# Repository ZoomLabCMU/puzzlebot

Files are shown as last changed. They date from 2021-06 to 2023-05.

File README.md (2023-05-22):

# PuzzleBots: Physical Coupling of Robot Swarms
Sha Yi, Zeynep Temel, Katia Sycara

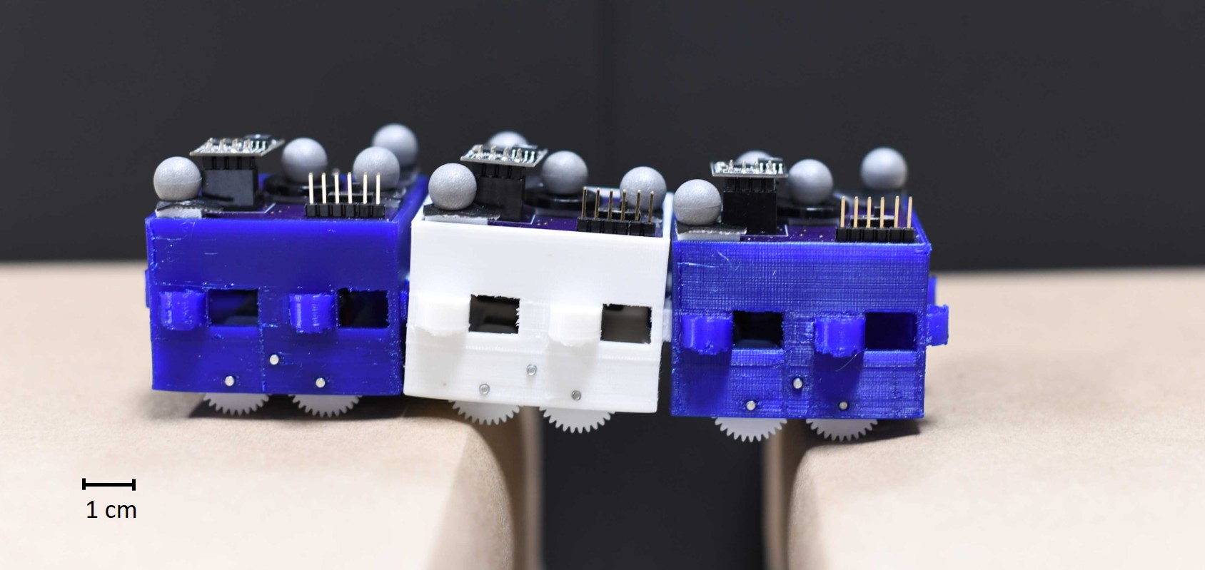
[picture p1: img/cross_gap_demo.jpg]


Link to our [video](https://www.youtube.com/watch?v=QP3eMZXLSw4). We present a guide to make and run our PuzzleBots. A newer version is available [here](https://github.com/ZoomLabCMU/puzzlebot_v2).  

If you find our work useful, please consider citing our paper:  
```
@inproceedings{yi2021puzzlebots,
  title={PuzzleBots: Physical Coupling of Robot Swarms},
  author={Yi, Sha and Temel, Zeynep and Sycara, Katia},
  booktitle={2021 IEEE International Conference on Robotics and Automation (ICRA)},
  pages={8742--8748},
  year={2021},
  organization={IEEE}
}
```

**Software Requirement**
- python
- ROS
- Arduino

**Hardware Requirement**
- 3D Printer
- Soldering Iron
- Circuit Board Production (may use external manufacturer)
- Vicon (or other localization systems)

## Preparation
1. Assemble the robot based on instructions from the [assembly page](docs/assembly.md).
2. Burn bootloader of Arduino Pro Mini (8M, 3.3V) to the ATMega328P.
3. Configure ESP8266 WiFi module with baud rate to be 9600.

## Run the Demo
### Setup
1. Configure the system  
Change Line 83 and 105 in `code/puzzlebot_arduino/wifitcp_motor_only/wifitcp_motor_only.ino` to your own wifi and IP address.
2. Load program onto circuit board  
Open the program `code/puzzlebot_arduino/wifitcp_motor_only/wifitcp_motor_only.ino` in Arduino Studio (or other Software) and load to the circuit board built in [assembly page](docs/assembly.md).
3. Build ROS package  
Copy `code/puzzlebot_control/` into the ROS catkin source directory. Build the package.

### Run
Each robot is associated with an IP address. In our setting, robot IP address has the form `192.168.0.20[ROBOT_ID]`. The corresponding Vicon ROS topic thus has the form `vicon/p20[ROBOT_ID]/p20[ROBOT_ID]`. For example, robot #2 has an IP of `192.168.0.202`, and the corresponding vicon topic is `vicon/p202/p202`.  
This can be changed in `code/puzzlebot_control/src/puzzlebot_control/hardware_wrap.py` Line 33. To turn off the vicon callback, change Line 30 in the `hardware_wrap.py` file.

Before launching the puzzlebot node, make sure the Vicon (or other localization system) is running and publishing the corret ROS topics. Then do
```
rosrun puzzlebot_control run_hardware.py [NUMBER_OF_ROBOTS]
```
For example, with three robots, run `rosrun puzzlebot_control run_hardware.py 3`.

Then, switch on the robots by sliding the switch on the top. You are expected to see the ESP8266 LED flashes then the console will show robots are connected in sequence. The program will start once all robots are connected.

### Testing Functions
A testing function `keyboard_input_lr` is provided in `robot.py`. It can be called in `hardware_wrap.py` to send velocity command during runtime to the robots to help debug hardware issues.

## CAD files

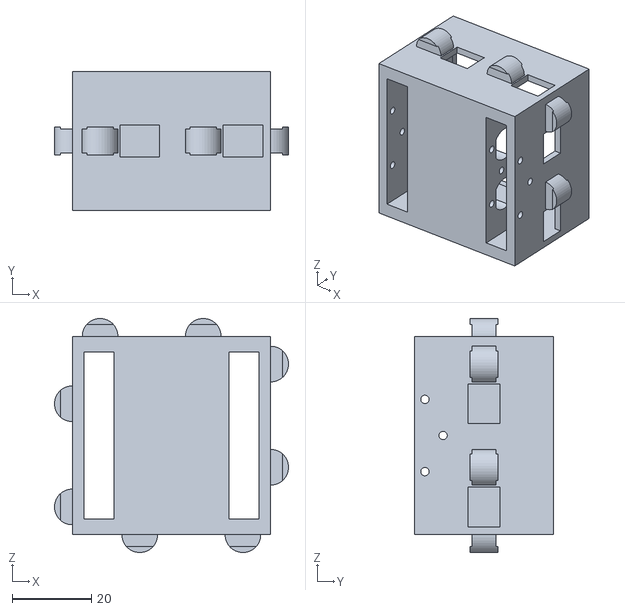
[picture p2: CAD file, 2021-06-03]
files/puzzlebot_chasis.STL
59.0 x 35.0 x 59.0

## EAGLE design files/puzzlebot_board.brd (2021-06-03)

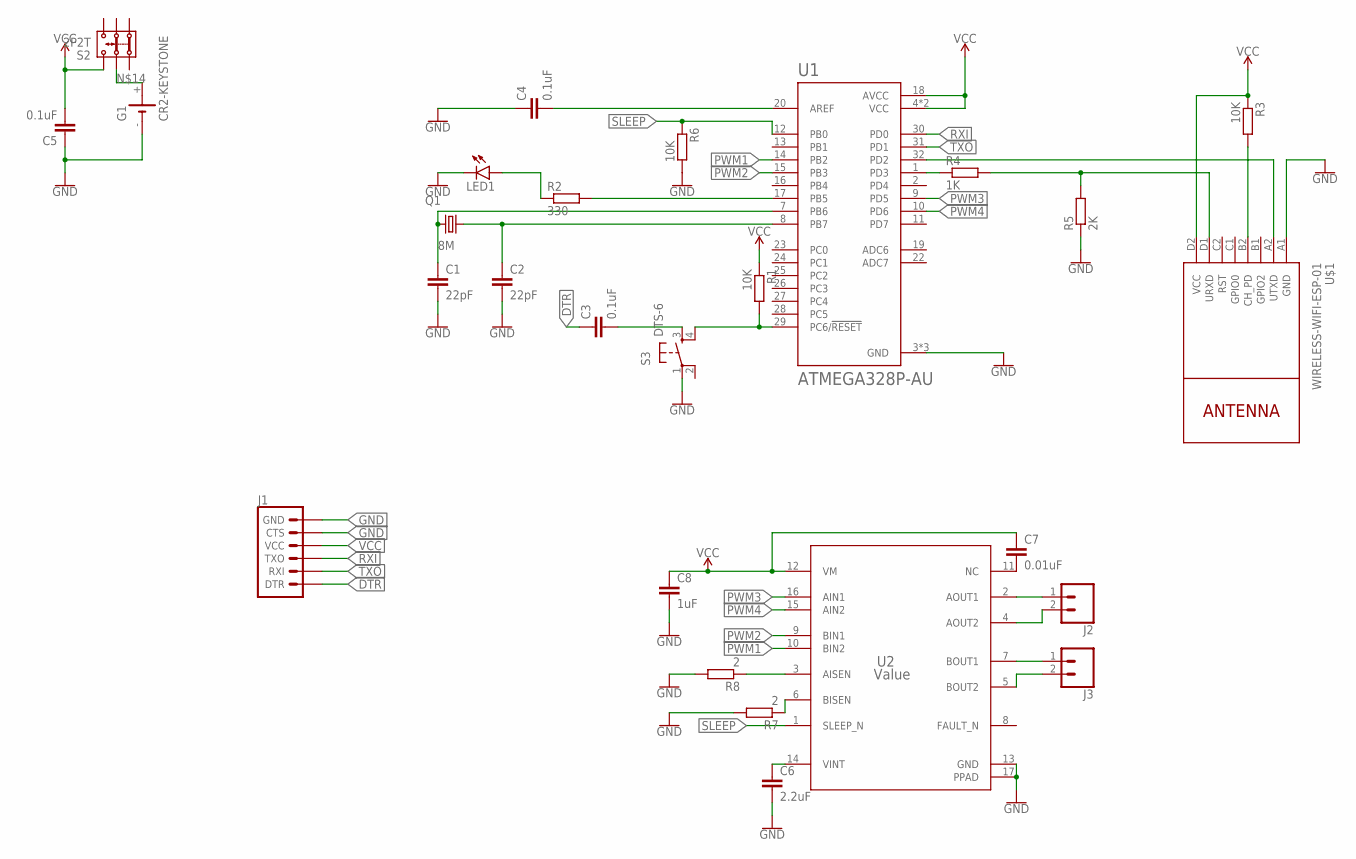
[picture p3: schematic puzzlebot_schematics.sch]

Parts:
C1, C2: 22pF; C0603
C3, C4, C5: 0.1uF; C0603
C6: 2.2uF; C0603
C7: 0.01uF; C0603
C8: 1uF; C0603
G1: CR2-KEYSTONE; SL-150-1/2AA/PR
J1: 6_PIN_SERIAL_TARGETLONGPADS; 1X06_LONGPADS
J2, J3: CONN_02POLAR; MOLEX-1X2
LED1: LEDCHIP-LED0805; CHIP-LED0805
Q1: 8M; CSM-7X-DU
R1, R3, R6: 10K; R0603
R2: 330; R0603
R4: 1K; R0603
R5: 2K; R0603
R7, R8: 2; R0603
S2: 2P2T
S3: DTS-6
U1: ATMEGA328P-AU; QFP80P900X900X120-32N
U2: Value; PWP0016K_M
U$1: WIRELESS-WIFI-ESP-01

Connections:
DTR: C3.1, J1.1 (DTR)
GND: C1.2, C2.2, C4.1, C5.1, C6.2, C8.2, G1.-, J1.5 (CTS), J1.6 (GND), LED1.C, R5.1, R6.2, R7.2, R8.2, S3.1, U1.3 (GND), U1.5 (GND), U1.21 (GND), U2.13 (GND), U2.17 (PPAD), U$1.A1 (GND)
unnamed: C2.1, Q1.2, U1.8 (PB7)
unnamed: C1.1, Q1.1, U1.7 (PB6)
unnamed: C3.2, S3.3
unnamed: R1.2, S3.4, U1.29 (PC6/!RESET)
unnamed: R3.2, U$1.B2 (CH_PD)
unnamed: R2.2, U1.17 (PB5)
unnamed: LED1.A, R2.1
unnamed: C4.2, U1.20 (AREF)
unnamed: U1.32 (PD2), U$1.A2 (UTXD)
unnamed: R4.1, U1.1 (PD3)
unnamed: R4.2, R5.2, U$1.D1 (URXD)
unnamed: C6.1, U2.14 (VINT)
unnamed: C7.2, U2.11 (NC)
unnamed: G1.+, S2.2.1
unnamed: R7.1, U2.6 (BISEN)
unnamed: R8.1, U2.3 (AISEN)
unnamed: J2.1, U2.2 (AOUT1)
unnamed: J3.1, U2.7 (BOUT1)
unnamed: J2.2, U2.4 (AOUT2)
unnamed: J3.2, U2.5 (BOUT2)
PWM1: U1.14 (PB2), U2.10 (BIN2)
PWM2: U1.15 (PB3), U2.9 (BIN1)
PWM3: U1.9 (PD5), U2.16 (AIN1)
PWM4: U1.10 (PD6), U2.15 (AIN2)
RXI: J1.3 (TXO), U1.30 (PD0)
SLEEP: R6.1, U1.12 (PB0), U2.1 (SLEEP_N)
TXO: J1.2 (RXI), U1.31 (PD1)
VCC: C5.2, C7.1, C8.1, J1.4 (VCC), R1.1, R3.1, S2.3.1, U1.4 (VCC), U1.6 (VCC), U1.18 (AVCC), U2.12 (VM), U$1.D2 (VCC)

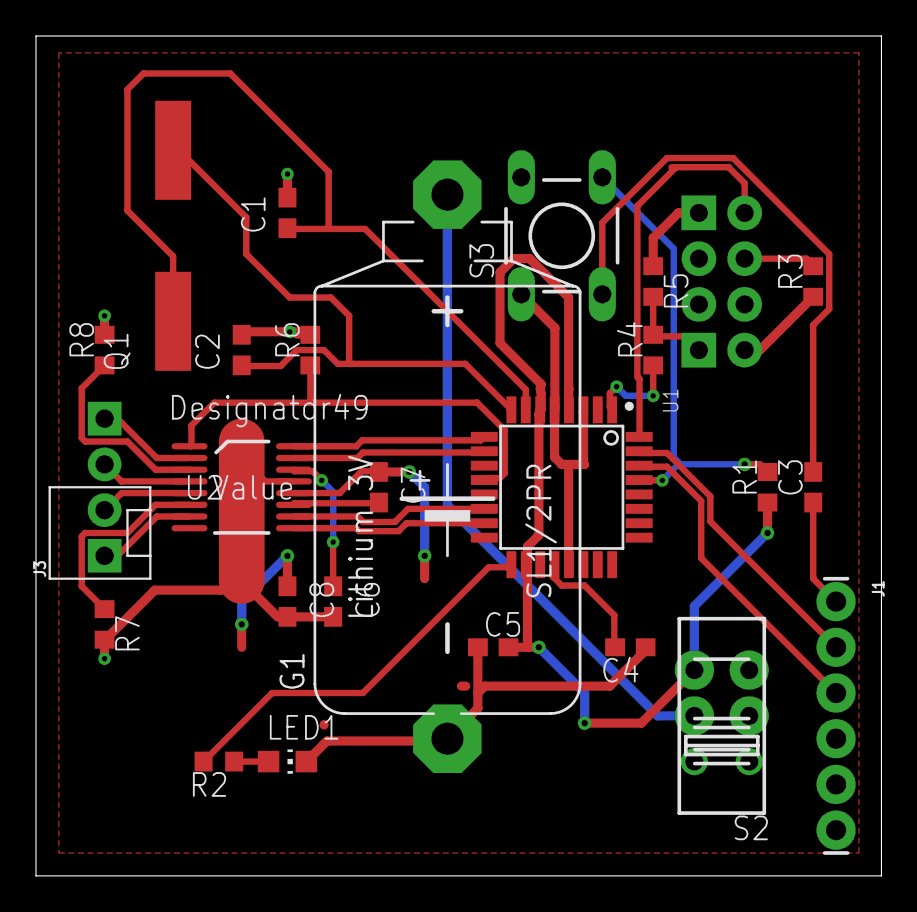
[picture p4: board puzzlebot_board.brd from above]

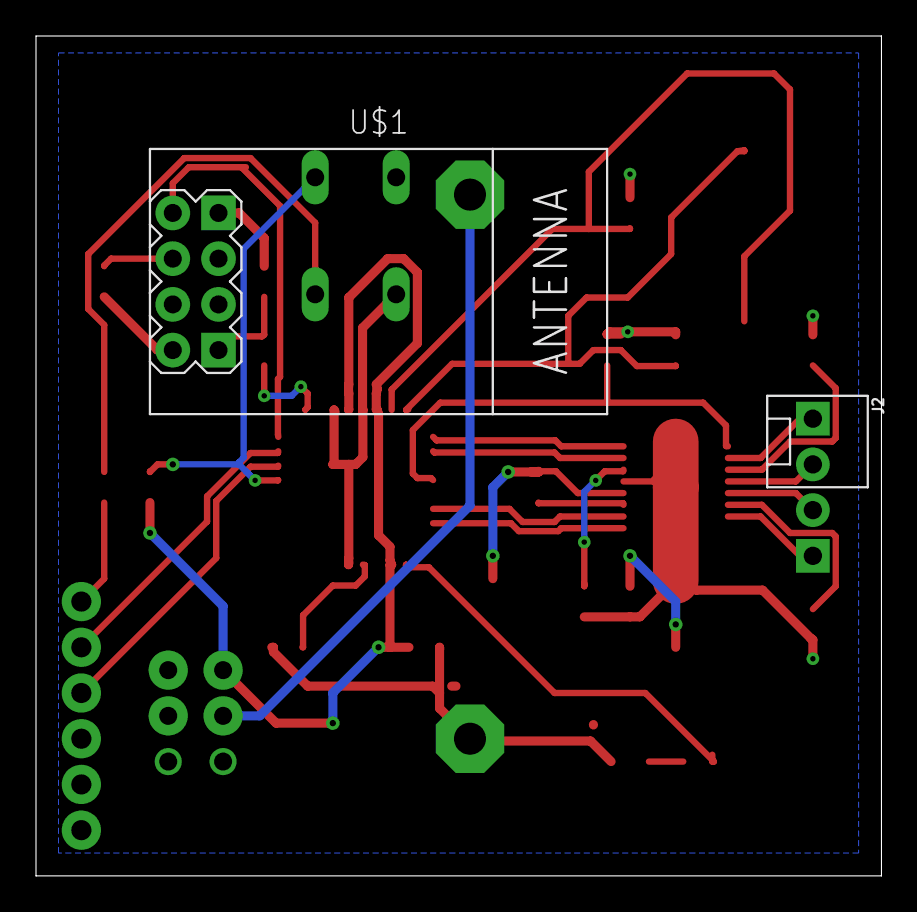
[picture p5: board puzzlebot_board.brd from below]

Board: 2 copper layers, 47.0 x 46.7 mm, 27 parts (2 on the bottom side), 30 nets.

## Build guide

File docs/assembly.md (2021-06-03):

# Assemble the robot

## Electronics
The circuit schematics `puzzlebot_schematics.sch` and board layout `puzzlebot_board.brd` are included in [`files/`](/files/).  
A full list of components:
- MCU ATMega328P x1
- 8M Oscillator x1
- Resistors (0603)
    - 2 Ohm x2
    - 330 Ohm x1
    - 1k Ohm x1
    - 2k Ohm x1
    - 10k Ohm x3
- Capacitors (0603)
    - 22 pF x2
    - 0.01 uF x1
    - 0.1 uF x3
    - 2.2 uF x1
- Battery CR2 x1
- WiFi Module ESP8266 x1
- Motor Driver DRV8833 x2
- Others
    - 6 pin on-on switch x1
    - 4 pin tactile switch x1
    - 0603 LED x1
    - 4 pin female header x2
    - 6 pin male header x1
    - CR2 battery holder x1

## 3D Printing
The robot body STL file can be found at [`files/puzzlebot_chasis.STL`](/files/puzzlebot_chasis.STL). Any 3D printer can be used. We used __Prusa__ with 0.15 mm precision, with NinjaFlex Cheetah filament. Support is generated with NinjaFlex material and removed after printing.

## Assembly
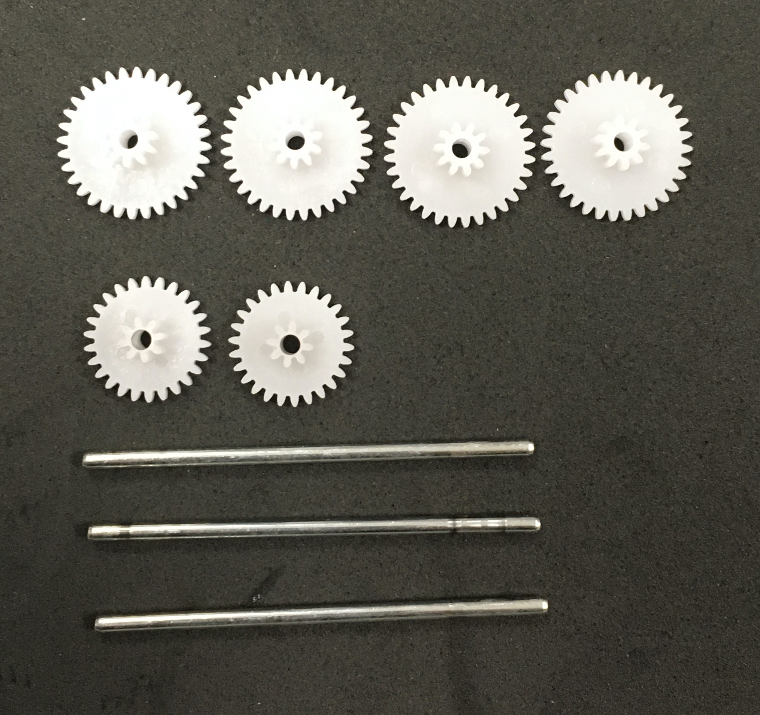
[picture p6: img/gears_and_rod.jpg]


Robot body includes: 
- 3D printed robot chasis 
- 50 mm rods x3
- 32-10 Module 0.5 gears x4
- 26-08 Module 0.5 gears x2

Assemble the above mentioned parts as shown:
<p float="left">
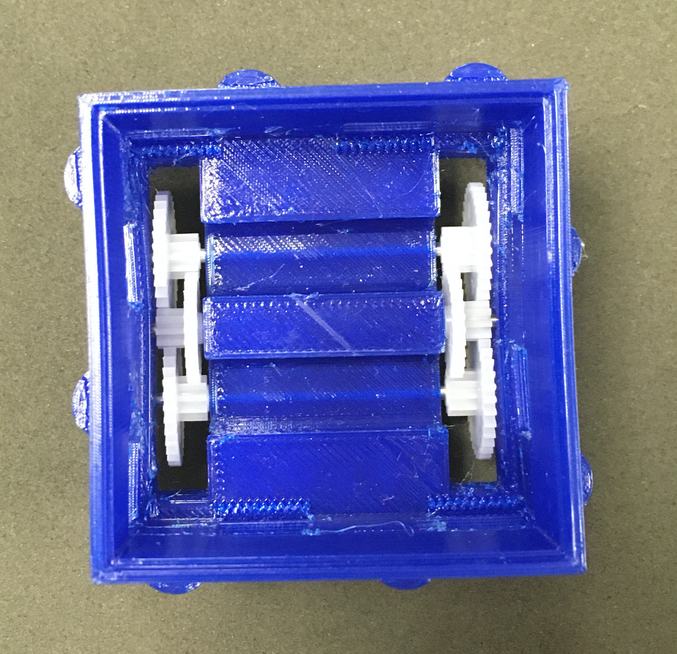
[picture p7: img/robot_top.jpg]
   
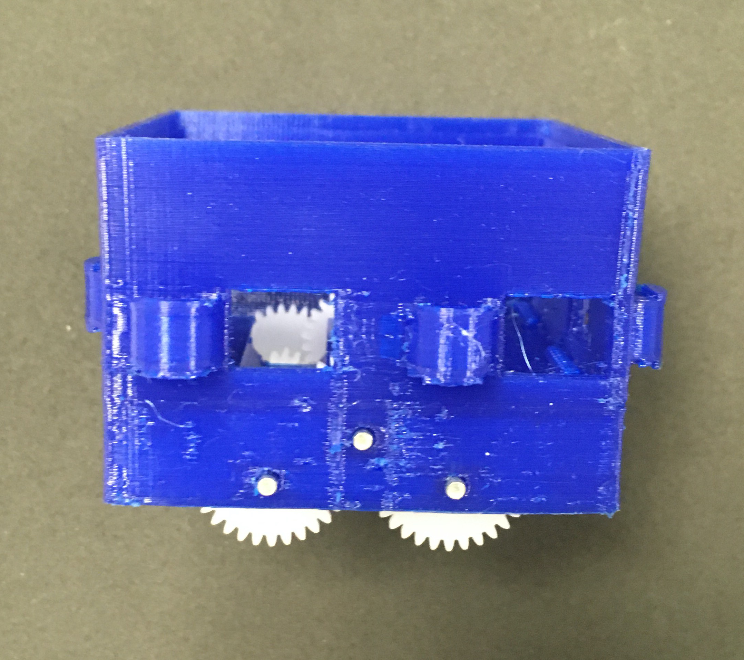
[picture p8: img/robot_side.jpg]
  
</p>

Attach the circuit board and tracking markers (a print of different color): 

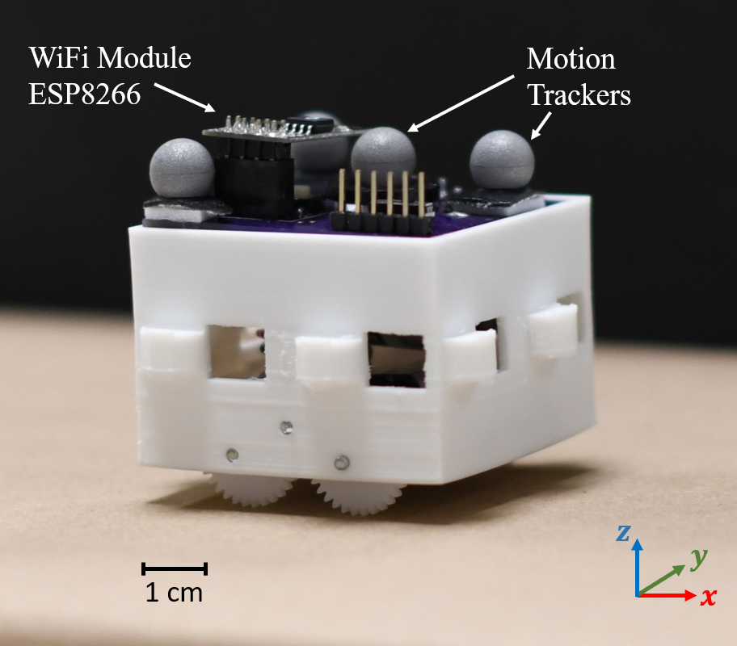
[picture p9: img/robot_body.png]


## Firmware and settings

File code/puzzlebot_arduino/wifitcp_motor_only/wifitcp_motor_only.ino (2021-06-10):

#include <SoftwareSerial.h>

#define INITIAL_STATUS 0
#define WIFI_CONNECTED 1
#define WIFI_INFO_PRINT 2
#define WIFI_TCP_CONNECT 3
#define WIFI_TCP_SENT 4
#define WIFI_TCP_NOTSENT 5

// robot hardware params
#define BODY_LENGTH 0.05f
#define WHEEL_RADIUS 0.01f
#define VLIM 0.2f
#define WLIM 0.5f
#define MOTOR_ULIM 120
#define MOTOR_LLIM 0

#define V_COEFF 1.2
#define W_COEFF 5.0

#define SERIAL_FLAG 0

SoftwareSerial EspSerial(2, 3); // RX, TX
int stat = INITIAL_STATUS;
String ip_addr = "";

int v_l = 0; int v_r = 0;
int lm_value = 0; int rm_value = 0;
int prev_l = 0; int prev_r = 0;
const float s_coeff = 0.5;

int right_fr = 10; int right_bk = 11;
int left_fr = 5; int left_bk = 6;
int sleep_pin = 8;
float l_coeff = 1; float r_coeff = 1;

bool tmp = 1;

void setup() {
  stat = INITIAL_STATUS;
  // set up pwm
  pinMode(left_fr, OUTPUT);
  pinMode(left_bk, OUTPUT);
  pinMode(right_fr, OUTPUT);
  pinMode(right_bk, OUTPUT);
  pinMode(sleep_pin, OUTPUT);
    
  digitalWrite(sleep_pin, HIGH);
  delay(10);
  
  if(SERIAL_FLAG) {
    Serial.begin(9600);
    delay(1000);
    Serial.println("System started");
  }
  // your esp's baud rate might be different 9600, 57600, 76800 or 115200
  EspSerial.begin(9600); 
  delay(2000);

  // check if it's already connected
  if(EspSerial.available()) {
    String s = EspSerial.readString();
    if(SERIAL_FLAG)
      Serial.print(s);
    if(s.indexOf("WIFI CONNECTED") >= 0) {
      stat = WIFI_CONNECTED;
    } else if(s.indexOf("WIFI GOT IP") >= 0) {
      stat = WIFI_CONNECTED;
    }
  } else {
    stat = INITIAL_STATUS;
  }
  checkEspMsg();
  if(SERIAL_FLAG) {
    Serial.print("state: "); Serial.println(stat);
  }
  delay(1000);

  while(stat != WIFI_CONNECTED) {
    if(SERIAL_FLAG)
      Serial.println("Trying to connect to internet...");
      EspSerial.print("AT+CWJAP=\"YOUR_WIFI\",\"YOUR_PASSWORD\"\r\n");
    while(!EspSerial.available()) {delay(10);}

    while(EspSerial.available())
    {
      String s = EspSerial.readString();
      if(SERIAL_FLAG)
        Serial.print(s);
      if(s.indexOf("WIFI CONNECTED") >= 0) {
        stat = WIFI_CONNECTED;
      } else if(s.indexOf("WIFI GOT IP") >= 0) {
        stat = WIFI_CONNECTED;
      }
    }
    delay(100);
  }
  checkEspMsg();
  if(SERIAL_FLAG)
    Serial.println("Connected to network");
  delay(100);

  while(stat != WIFI_TCP_CONNECT) {
    EspSerial.print("AT+CIPSTART=\"TCP\",\"YOUR_COMPUTER_IP\",8080\r\n");
    while(!EspSerial.available()) {delay(10);}
    while(EspSerial.available()) {
      String s = EspSerial.readString();
      if(SERIAL_FLAG)
        Serial.print(s);
      if(s.indexOf("\nOK") >= 0 || s.indexOf("CONNECT") >= 0) {
        stat = WIFI_TCP_CONNECT;
      }
      if(s.indexOf("WIFI GOT IP") >= 0) {
        stat = WIFI_CONNECTED;
      }
    }
    delay(50);
  }
  checkEspMsg();
  if(SERIAL_FLAG)
    Serial.println("Connected to TCP port");
  delay(500);
}
 
void loop() {
  while(!getValueFromMsg(v_l, v_r)) {
    tmp = !tmp;
  }
  computeMotor(v_l, v_r);
  delay(1);
  while(!sendMotorData()) {
    tmp = !tmp;
  }
}

void computeMotor(int v_l, int v_r) {
  writeMotor(v_l, 0); writeMotor(v_r, 1);
}

void writeMotor(int m_vel, int lr_flag) {
  // lr_flag = 0 (left), = 1 (right)

  if(m_vel > MOTOR_ULIM) {
    m_vel = MOTOR_ULIM;
  } else if(m_vel < -MOTOR_ULIM) {
    m_vel = -MOTOR_ULIM;
  } else if(m_vel > 0.01 && m_vel < MOTOR_LLIM) {
    m_vel = MOTOR_LLIM;
  } else if(m_vel < -0.01 && m_vel > -MOTOR_LLIM) {
    m_vel = -MOTOR_LLIM;
  }

  if(lr_flag == 0) {
    lm_value = m_vel;
  } else {
    rm_value = m_vel;
  }
  stat = WIFI_TCP_NOTSENT;
  
  if(lr_flag == 0 && m_vel >= 0) {
    analogWrite(left_fr, m_vel);
    analogWrite(left_bk, 0);
  } else if(lr_flag == 0 && m_vel < 0) {
    analogWrite(left_bk, - m_vel);
    analogWrite(left_fr, 0);
  } else if(lr_flag == 1 && m_vel >= 0) {
    analogWrite(right_fr, m_vel);
    analogWrite(right_bk, 0);
  } else if(lr_flag == 1 && m_vel < 0) {
    analogWrite(right_bk, - m_vel);
    analogWrite(right_fr, 0);
  }
}

bool getValueFromMsg(int& v_l, int& v_r) {
  // expect input msg format to be "[v left],[v right]", integer
  
  String value_str = "";
  while(!EspSerial.available()) {tmp=!tmp;}
  if(EspSerial.available()) {
    String s = "";
    while(EspSerial.available()) {
      // The esp has data so display its output to the serial window 
      char c = EspSerial.read(); // read the next character.
      if(c == '\n') break;
      s += c;
    }
    
    if(s.indexOf("+IPD") < 0 || s.indexOf(':') < 0) {
      if(SERIAL_FLAG) {
        Serial.print("wrong msg: "); Serial.println(s);
      }
      
      return false;
    }

    value_str = s.substring(s.indexOf(':')+1);
  }
  
  if(value_str.length() < 2) return false;

  int idx_com = value_str.indexOf(',');
  if(idx_com < 0) return false;

  String s_vec[2] = {value_str.substring(0, idx_com), value_str.substring(idx_com+1)};

  // pass by reference
  v_l = s_vec[0].toInt(); v_r = s_vec[1].toInt();
  return true;
}

void checkEspMsg() {
  if(EspSerial.available()) // check if the ESP module is sending a message 
  {
    while(EspSerial.available())
    {
      // The esp has data so display its output to the serial window 
      char c = EspSerial.read(); // read the next character.
      if(SERIAL_FLAG)
        Serial.write(c);
    }  
  }
}

bool sendMotorData() {
  if(stat != WIFI_TCP_NOTSENT) return false;
  if(EspSerial.available()) return false;

  EspSerial.print("AT+CIPSEND=9\r\n");

  String s = "";
  while(!EspSerial.available()) {tmp = !tmp;}

  while(EspSerial.available()) {
    char c = EspSerial.read(); // read the next character.
    s += c;
  }

  if(s.indexOf("OK") < 0) {
    return false;
  }

  // esp is now able to send data
  char buf[10] = {};
  sprintf(buf, "%04d,%04d\n", lm_value, rm_value);
  EspSerial.print(buf);
  stat = WIFI_TCP_SENT;

  while(!EspSerial.available()) {tmp = !tmp;}
  while(EspSerial.available()) {
    char c = EspSerial.read();
  }
  return true;
}

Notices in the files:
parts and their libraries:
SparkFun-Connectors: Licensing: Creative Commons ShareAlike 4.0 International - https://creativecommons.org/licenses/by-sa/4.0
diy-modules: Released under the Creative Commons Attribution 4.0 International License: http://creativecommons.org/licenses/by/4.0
